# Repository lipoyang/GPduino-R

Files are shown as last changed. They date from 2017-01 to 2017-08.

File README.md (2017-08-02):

GPduino-R
=========

## 概要
GPduino-Rは、ESP8266搭載のWiFiロボット制御ボードです。

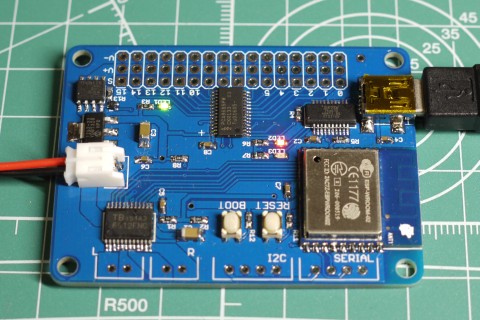
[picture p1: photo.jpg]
写真


以下のことができます。
* ラジコンサーボ最大16個を制御
* DCモータ2個を制御 (最大連続1.2A / 最大瞬間3.0A)
* 電源 3.6V～7.2V (4.8～6V推奨)、電源電圧を監視
* WiFiによる通信　(APにもSTAにもなれる)

## ファイル一覧

* hard/GPduino-R/
	* GPduino-R.sch/brd: 回路/基板設計データ(Eagle形式)
	* GPduino-R.pdf: 回路図(PDF)
	* GPduino-R_BOM.xlsx: BOMリスト(Excel形式)
	* GPduino-R.GBL/GBO/GBP/GBS/GML/GTL/GTO/GTP/GTS/TXT: ガーバデータ
* firm/
	* GPduinoR/: Arduinoライブライリ
	* Mini4LD/Mini4LD.ino: 四足歩行ロボットのArduinoスケッチ
* LICENSE: Apache Licence 2.0です。
	* ただし、回路/基板設計は、Creative Commons Attribution Share-Alike 3.0です。
* README.md これ

## Arduino開発環境のセットアップ
GPduino-R はESP8266を搭載しており、Arduinoでファームウェアを開発できます。

* まず、ArduinoIDE をインストールしておきます。 (ここでは 1.6.9 を使用)
* [ファイル] > [環境設定] > [Additional Boards Manager URLs:]に下記URLをコピペ
	* http://arduino.esp8266.com/stable/package_esp8266com_index.json (安定版)
	* http://arduino.esp8266.com/staging/package_esp8266com_index.json (開発版)
* [ツール] > [ボード] > [ボードマネージャ] で [esp8266] をインストール
* [ツール] > [ボード] で [Generic ESP8266 Module]を選択
	* Flash Mode : QIO
	* Flash Frequency : 40MHz
	* Upload Using : Serial
	* CPU Frequency : 80MHz
	* Flash Size : 4M(3M SPIFFS)　(3MBをファイルシステムで使用 / 1MBをスケッチで使用)
	* Debug port : Disabled
	* Debug Level : None
	* Reset Method : nodemcu
	* Upload Speed : 115200

## Arduinoライブラリのインストール

firm/ にある GPduinoR/ フォルダを、Arduinoのライブラリフォルダにコピーします。

Arduinoのライブラリフォルダは、以下の場所です。
* Documents/Arduino/libraries (Windows10, Mac, Linux)
* My Documents/Arduino/libraries (Windows7)

## Arduinoスケッチの作成
GPduinoR.h をインクルードします。
``` c
#include <GPduinoR.h>
```
すると、以下のオブジェクトが使用できます。詳細は、GPduinoR/フォルダにあるソースを参照してください。
- Battery: バッテリー電圧の取得
- DcMotor: DCモータの制御
- RcServo: ラジコンサーボの制御
- UdpComm: WiFiによるUDP/IP通信

Mini4LD/Mini4LD.ino は、四足歩行ロボット([歩くミニ四駆](https://www.youtube.com/watch?v=Bx3RYRKqrKQ))のArduinoスケッチです。参考にしてください。

## Arduinoスケッチの書き込み

* GPduino-RをUSBケーブルでPCに接続します。
* 書き込み時もUSBからの給電は受けません。CN1から給電してください。
* Windows 7以降であればドライバが自動でインストールされ、COMポートとして認識されます。
	* 自動でデバイスが認識されない環境ではFTDIのデバイスドライバをインストールしてください。
* [ツール] > [シリアルポート]でGPduino-RのCOMポート番号を指定します。
* BOOTボタン(SW2)を押し下げた状態で、RESETボタン(SW1)を押して離します。
* Uploadボタンで、ファームウェアを書き込みます。

## 既知の問題点
* サーボのコネクタの間隔が狭すぎる。(干渉して16個全部を接続できない)

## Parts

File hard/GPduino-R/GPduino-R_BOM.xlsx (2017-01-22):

No | Reference | Part Number | Vender | Description | DNP | Qty | Unit Price | Price | Lot Size | Supplier | Supplier Code
1 | C1,3 | 47u(3216) | (generic) | 3216型 |  | 2 | 30 | 60 | 10 | 秋月 | P-06040
2 | C2,4,5,6,7,8 | 0.1u(1608) | (generic) | 1608型 |  | 6 | 0.325 | 1.95 | 4000 | 秋月 | P-01299
3 | CN1 | S2B-PH-K-S | JST | PH 2極 L型ポスト |  | 1 | 16 | 16 | 1 | 共立 | -
4 | CN2,3 | B2B-EH-A | JST | EH 2極 I型ポスト | DNP | 0 | 16 | 0 | 1 | 共立 | -
5 | CN4 | MINI-USB-UX60A-MB-5ST | HRS | USB ミニB |  | 1 | 50 | 50 | 4 | 秋月 | C-05690
6 | CN5,6 | B4B-EH-A | JST | EH 4極 I型ポスト | DNP | 0 | 21 | 0 | 1 | 共立 | -
7 | CN7,8,9,10 | - | (generic) | ピンヘッダ 3ピン×4 | DNP | 0 | 60 | 0 | 2 | 共立 | -
8 | LED1 | OSYG1608 | OptoSupply | 1608型 GREEN |  | 1 | 10 | 10 | 20 | 秋月 | I-03980
9 | LED2 | OSHR1608 | OptoSupply | 1608型 RED |  | 1 | 10 | 10 | 20 | 秋月 | I-03978
10 | LED3 | OSYL1608 | OptoSupply | 1608型 YELLOW |  | 1 | 10 | 10 | 20 | 秋月 | I-03984
11 | Q1 | DTC014EEB | ROHM | NPNデジタルトランジスタ |  | 1 | 3.2 | 3.2 | 200 | RS | 124-6536
12 | Q2 | TPC8125 | Toshiba | PMOS FET |  | 1 | 36.8 | 36.8 | 5 | RS | 756-3817
13 | R1 | 100k(1608) | (generic) | 1608型 |  | 1 | 0.2 | 0.2 | 2500 | 秋月 | R-06104
14 | R2,5,8,11,12,13 | 10k(1608) | (generic) | 1608型 |  | 6 | 0.2 | 1.2 | 2500 | 秋月 | R-06103
15 | R3 | 220(1608) | (generic) | 1608型 |  | 1 | 0.2 | 0.2 | 2500 | 秋月 | R-06221
16 | R4,R6,R7 | 1k(1608) | (generic) | 1608型 |  | 3 | 0.2 | 0.6 | 2500 | 秋月 | R-06102
17 | R9,R10 | 10k(1608) | (generic) | 1608型 | DNP | 0 | 0.2 | 0 | 2500 | 秋月 | R-06103
18 | SW1,2 | SKRPACE010 | ALPS | 表面実装タクトスイッチ |  | 2 | 20 | 40 | 5 | 秋月 | P-06185
20 | U1 | TC1262-3.3VDB05MP | Microchip | LDO, 3.3V-0.5A, SOT-223型 |  | 1 | 81 | 81 | 1 | RS | 703-7905
21 | U2 | TB6621FNG | Toshiba | Dual DCモータドライバ |  | 1 | 306 | 306 | 1 | RS | 770-3797
22 | U3 | FT231XS | FTDI | USBシリアル変換 |  | 1 | 210 | 210 | 1 | 秋月 | I-06713
23 | U4 | ESP-WROOM-02 | Espressif Systems | ESP8266 WiFiモジュール |  | 1 | 550 | 550 | 1 | 秋月 | M-09607
24 | U5 | PCA9685PW | NXP | PWMドライバ |  | 1 | 262 | 262 | 2 | RS | 727-5649
25 | - | - | Elecrow | 基板 |  | 1 | 260.1 | 260.1 | 10 | Elecrow | -
26 | - | PH2P300L | Marutsu | PH 2極 アッセンブルケーブル |  | 1 | 54 | 54 | 1 | マルツ | -
 |  |  |  |  |  |  | Total | 1963.25

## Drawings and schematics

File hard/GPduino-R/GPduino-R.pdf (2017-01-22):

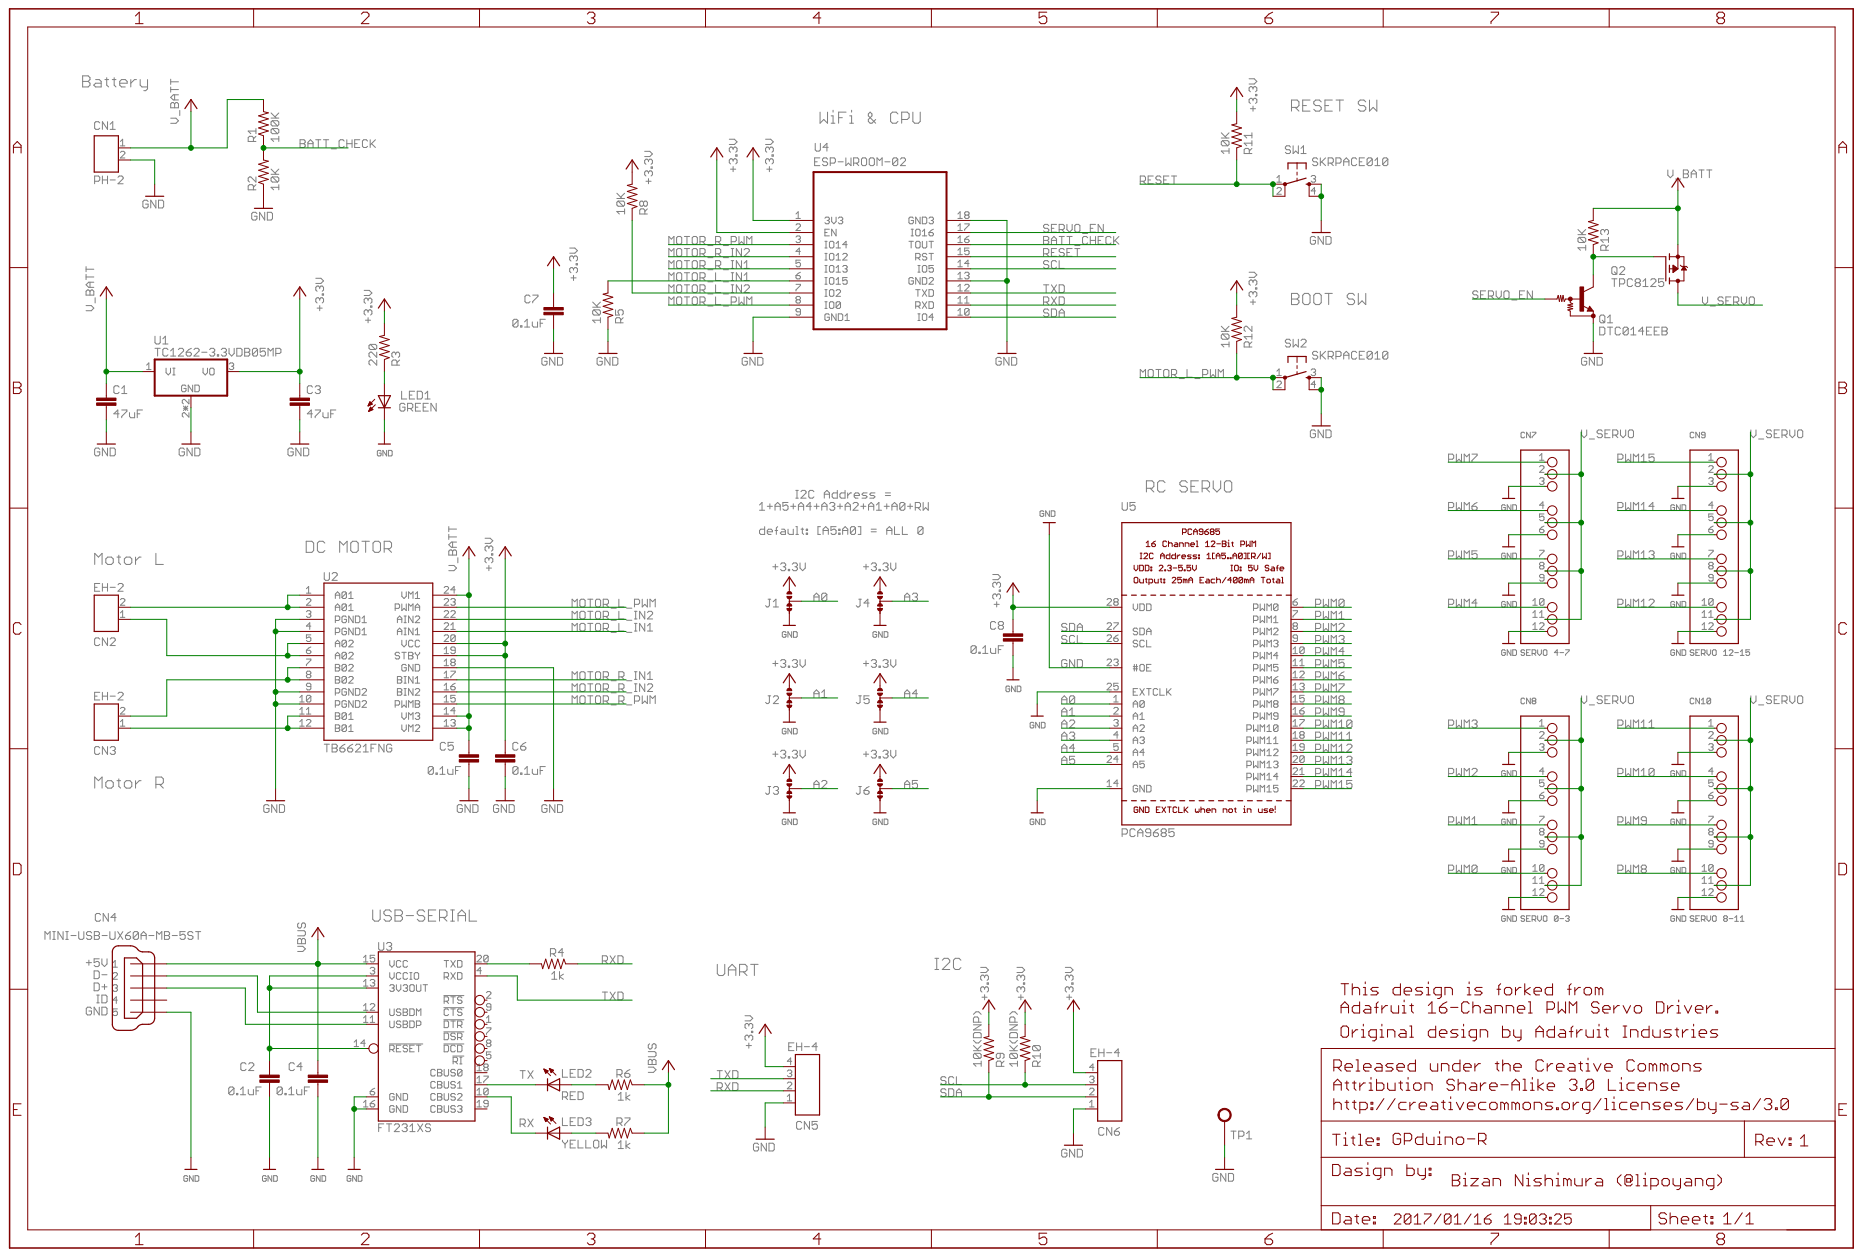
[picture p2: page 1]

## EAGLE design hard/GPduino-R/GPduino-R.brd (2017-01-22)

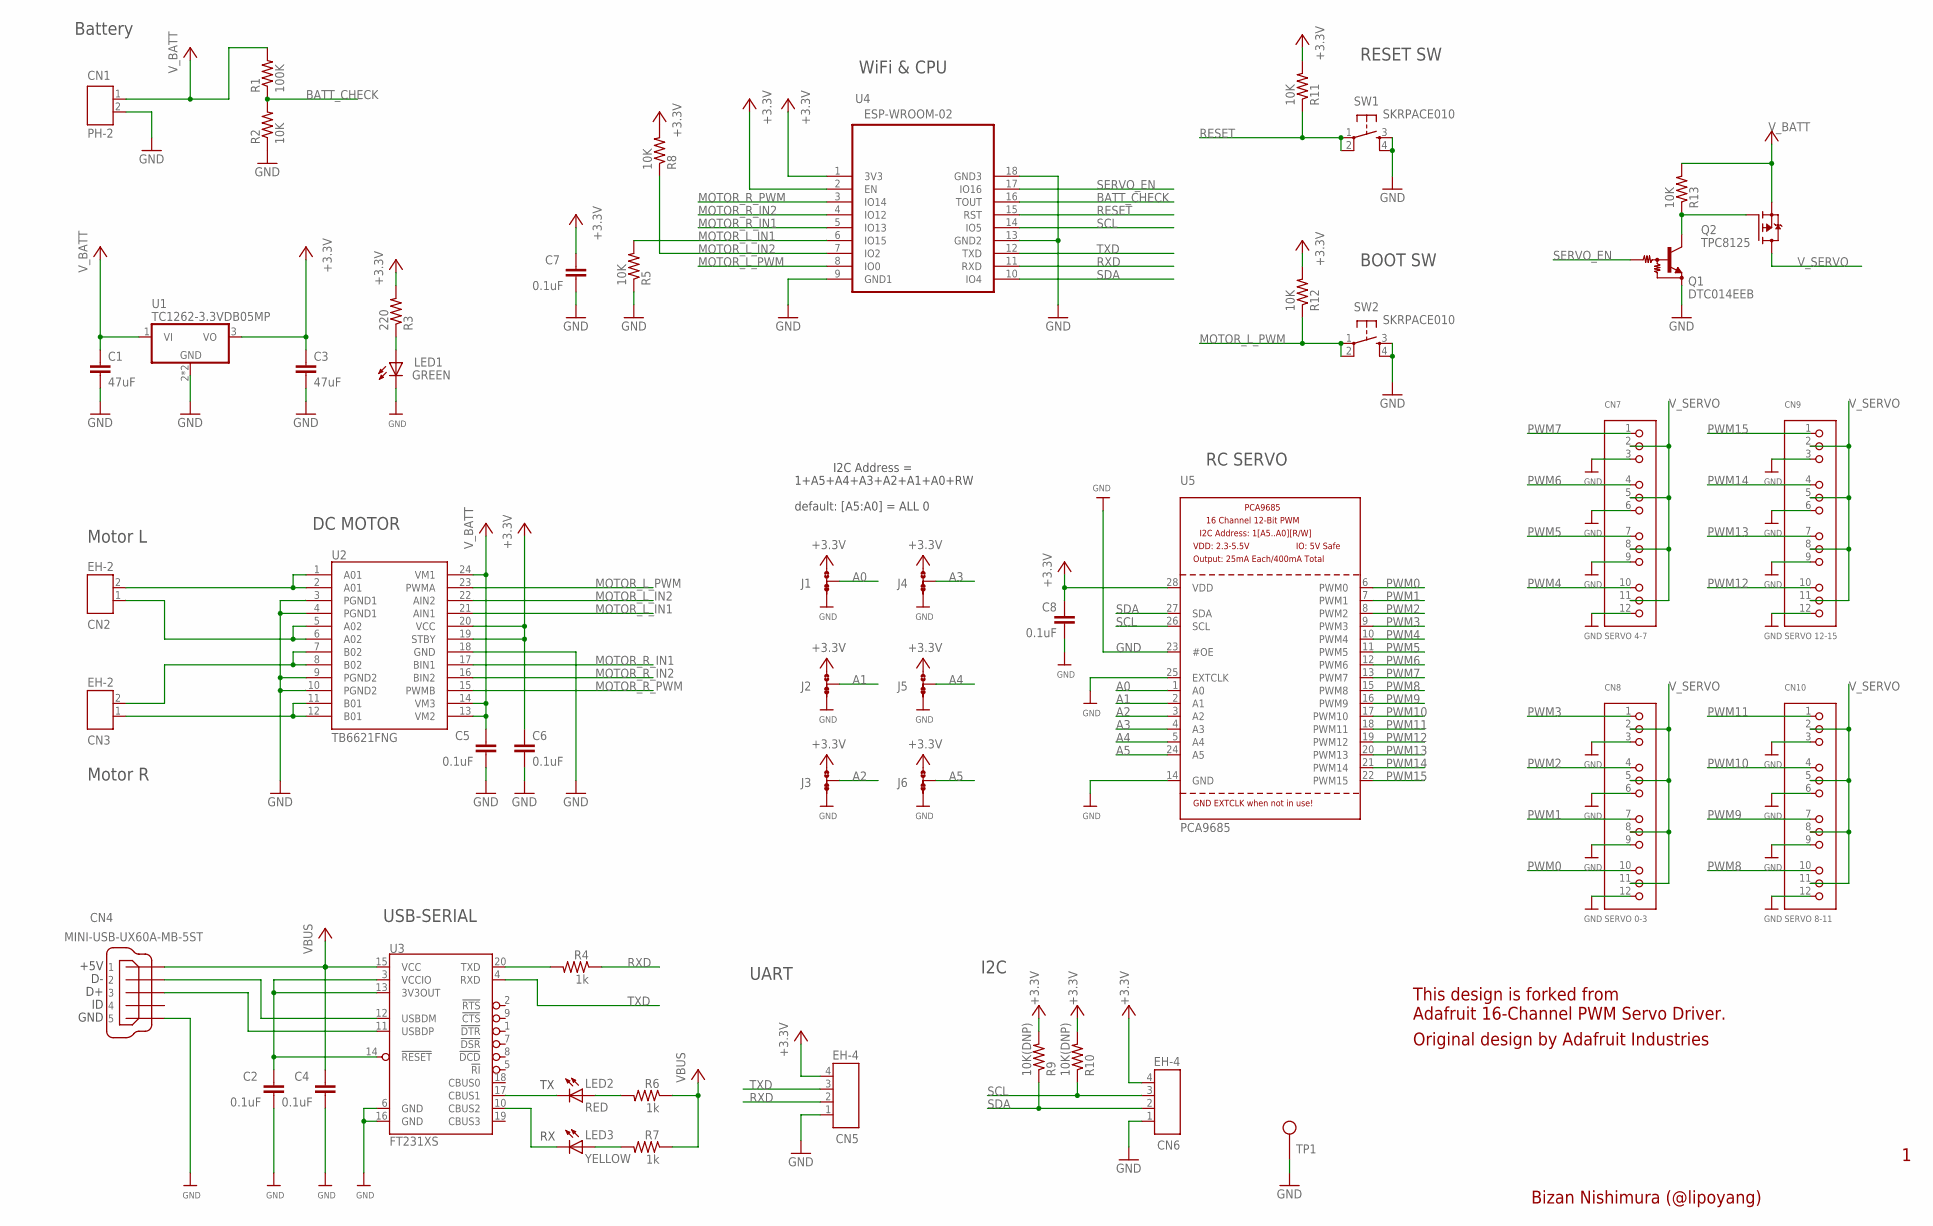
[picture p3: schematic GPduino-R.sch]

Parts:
C1, C3: 47uF; C3216
C2, C4, C5, C6, C7, C8: 0.1uF; C1608
CN1: PH-2
CN2, CN3: EH-2
CN4: MINI-USB-UX60A-MB-5ST; UX60A-MB-5ST
CN5, CN6: EH-4
CN7: SERVO 4-7; 3X04
CN8: SERVO 0-3; 3X04
CN9: SERVO 12-15; 3X04
CN10: SERVO 8-11; 3X04
J1, J2, J3, J4, J5, J6: JUMP-SHORTB; JUMP-SHORT
LED1: GREEN; CHIPLED_0603
LED2: RED; CHIPLED_0603
LED3: YELLOW; CHIPLED_0603
Q1: DTC014EEB; SOT490
Q2: TPC8125; SO-8
R1: 100K; 0603-RES
R2, R5, R8, R11, R12, R13: 10K; 0603-RES
R3: 220; 0603-RES
R4, R6, R7: 1k; 0603-RES
R9, R10: 10K(DNP); 0603-RES
SW1, SW2: SKRPACE010
TP1: TEST_PIN
U1: TC1262-3.3VDB05MP; SOT223
U2: TB6621FNG; SSOP24
U3: FT231XS; SSOP20
U4: ESP-WROOM-02; FRONT-FACE
U5: PCA9685; TSSOP28

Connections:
+3V3: C3.1, C6.1, C7.1, C8.1, CN5.4, CN6.4, J1.1, J2.1, J3.1, J4.1, J5.1, J6.1, R3.2, R8.2, R9.2, R10.2, R11.2, R12.2, U1.3 (VO), U2.19 (STBY), U2.20 (VCC), U4.1 (3V3), U4.2 (EN), U5.28 (VDD)
A0: J1.2, U5.1 (A0)
A01: CN2.2, U2.1 (A01), U2.2 (A01)
A1: J2.2, U5.2 (A1)
A02: CN2.1, U2.5 (A02), U2.6 (A02)
A2: J3.2, U5.3 (A2)
A3: J4.2, U5.4 (A3)
A4: J5.2, U5.5 (A4)
A5: J6.2, U5.24 (A5)
BATT_CHECK: R1.1, R2.2, U4.16 (TOUT)
GND: C1.2, C2.2, C3.2, C4.2, C5.2, C6.2, C7.2, C8.2, CN1.2, CN4.5, CN5.1, CN6.1, CN7.3, CN7.6, CN7.9, CN7.12, CN8.3, CN8.6, CN8.9, CN8.12, CN9.3, CN9.6, CN9.9, CN9.12, CN10.3, CN10.6, CN10.9, CN10.12, J1.3, J2.3, J3.3, J4.3, J5.3, J6.3, LED1.C, Q1.2 (E), R2.1, R5.1, SW1.3, SW1.4, SW2.3, SW2.4, TP1.1, U1.2 (GND), U1.4 (GND), U2.3 (PGND1), U2.4 (PGND1), U2.9 (PGND2), U2.10 (PGND2), U2.18 (GND), U3.6 (GND), U3.16 (GND), U4.9 (GND1), U4.13 (GND2), U4.18 (GND3), U5.14 (GND), U5.23 (#OE), U5.25 (EXTCLK)
MOTOR_L_IN1: R5.2, U2.21 (AIN1), U4.6 (IO15)
MOTOR_L_IN2: R8.1, U2.22 (AIN2), U4.7 (IO2)
MOTOR_L_PWM: R12.1, SW2.1, SW2.2, U2.23 (PWMA), U4.8 (IO0)
MOTOR_R_IN1: U2.17 (BIN1), U4.5 (IO13)
MOTOR_R_IN2: U2.16 (BIN2), U4.4 (IO12)
MOTOR_R_PWM: U2.15 (PWMB), U4.3 (IO14)
unnamed: LED1.A, R3.1
unnamed: R4.2, U3.20 (TXD)
unnamed: CN3.1, U2.11 (B01), U2.12 (B01)
unnamed: CN3.2, U2.7 (B02), U2.8 (B02)
unnamed: LED2.C, U3.17 (CBUS1)
unnamed: LED3.C, U3.10 (CBUS2)
unnamed: LED2.A, R6.2
unnamed: LED3.A, R7.2
unnamed: CN4.2, U3.12 (USBDM)
unnamed: CN4.3, U3.11 (USBDP)
unnamed: C2.1, U3.3 (VCCIO), U3.13 (3V3OUT), U3.14 (!RESET)
unnamed: Q1.3 (C), Q2.4 (G), R13.1
PWM0: CN8.10, U5.6 (PWM0)
PWM1: CN8.7, U5.7 (PWM1)
PWM2: CN8.4, U5.8 (PWM2)
PWM3: CN8.1, U5.9 (PWM3)
PWM4: CN7.10, U5.10 (PWM4)
PWM5: CN7.7, U5.11 (PWM5)
PWM6: CN7.4, U5.12 (PWM6)
PWM7: CN7.1, U5.13 (PWM7)
PWM8: CN10.10, U5.15 (PWM8)
PWM9: CN10.7, U5.16 (PWM9)
PWM10: CN10.4, U5.17 (PWM10)
PWM11: CN10.1, U5.18 (PWM11)
PWM12: CN9.10, U5.19 (PWM12)
PWM13: CN9.7, U5.20 (PWM13)
PWM14: CN9.4, U5.21 (PWM14)
PWM15: CN9.1, U5.22 (PWM15)
RESET: R11.1, SW1.1, SW1.2, U4.15 (RST)
RXD: CN5.2, R4.1, U4.11 (RXD)
SCL: CN6.3, R10.1, U4.14 (IO5), U5.26 (SCL)
SDA: CN6.2, R9.1, U4.10 (IO4), U5.27 (SDA)
SERVO_EN: Q1.1 (B), U4.17 (IO16)
TXD: CN5.3, U3.4 (RXD), U4.12 (TXD)
VBUS: C4.1, CN4.1, R6.1, R7.1, U3.15 (VCC)
V_BATT: C1.1, C5.1, CN1.1, Q2.1 (S), Q2.2 (S), Q2.3 (S), R1.2, R13.2, U1.1 (VI), U2.13 (VM2), U2.14 (VM3), U2.24 (VM1)
V_SERVO: CN7.2, CN7.5, CN7.8, CN7.11, CN8.2, CN8.5, CN8.8, CN8.11, CN9.2, CN9.5, CN9.8, CN9.11, CN10.2, CN10.5, CN10.8, CN10.11, Q2.5 (D), Q2.6 (D), Q2.7 (D), Q2.8 (D)

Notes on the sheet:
Battery
Motor L
Bizan Nishimura (@lipoyang)
Motor R
I2C
1+A5+A4+A3+A2+A1+A0+RW
I2C Address =
default: [A5:A0] = ALL 0
UART
USB-SERIAL
DC MOTOR
RC SERVO
WiFi & CPU
RESET SW
BOOT SW
This design is forked from Adafruit 16-Channel PWM Servo Driver.
Original design by Adafruit Industries

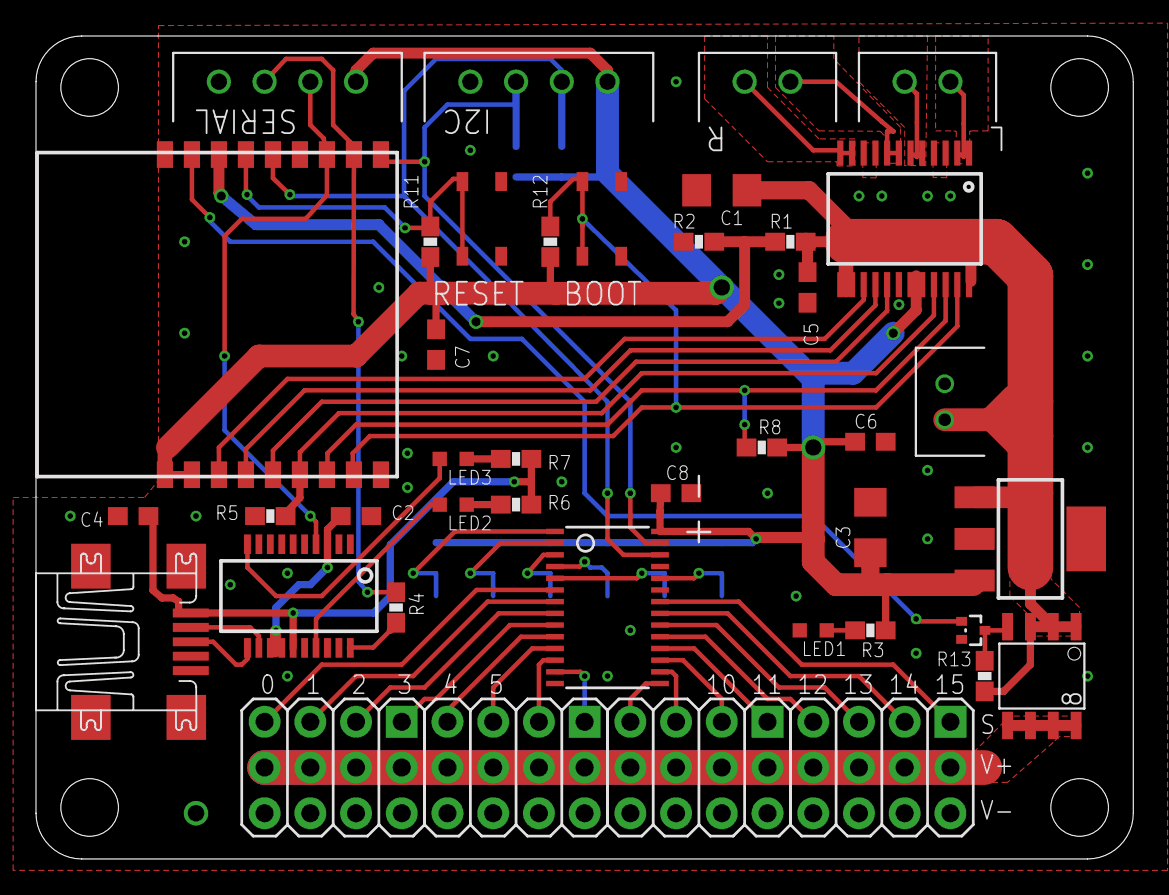
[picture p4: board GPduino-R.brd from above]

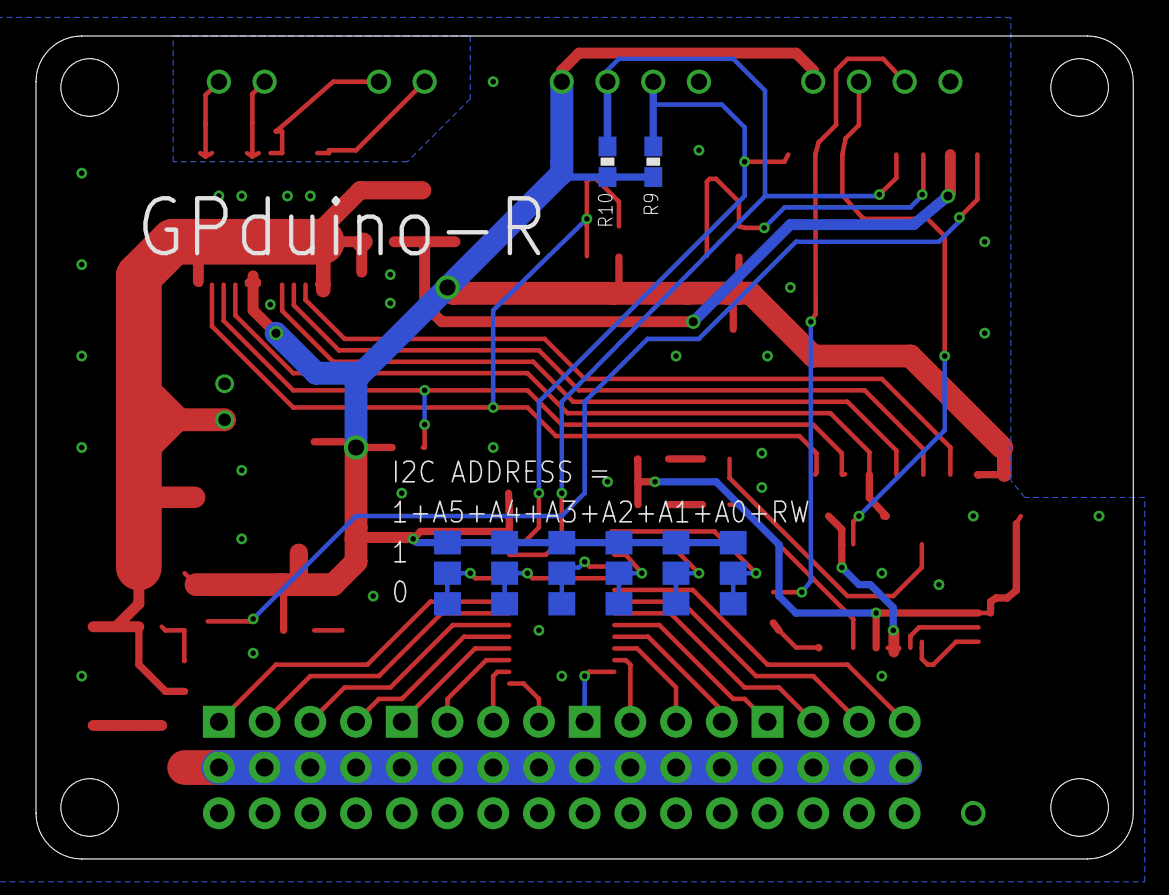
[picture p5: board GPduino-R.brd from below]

Board: 2 copper layers, 61.0 x 45.7 mm, 50 parts (8 on the bottom side), 54 nets.

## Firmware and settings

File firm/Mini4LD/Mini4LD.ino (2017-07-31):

#include <GPduinoR.h>

// サーボ番号
enum {
    SERVO_RF_Y = 0, // 右前股
    SERVO_RF_Z,     // 右前膝
    SERVO_LF_Y,     // 左前股
    SERVO_LF_Z,     // 左前膝
    SERVO_RB_Y,     // 右後股
    SERVO_RB_Z,     // 右後膝
    SERVO_LB_Y,     // 左後股
    SERVO_LB_Z,     // 左後膝
};
// サーボチャンネル開始番号
#define SERVO_BEGIN 8

// サーボの向きとゼロ点オフセット
static const int SERVO_POLARITY[]={
// 0:右前股 1:右前膝 2:左前股 3:左前膝 4:右後股 5:右後膝 6:左後股 7:左後膝
  -1,      -1,      +1,      +1,      -1,      +1,      +1,      -1
};
static const int SERVO_OFFSET[]={
// 0:右前股 1:右前膝 2:左前股 3:左前膝 4:右後股 5:右後膝 6:左後股 7:左後膝
  18,       0,     -14,       3,     -17,     -13,      22,       5
};

// 1コマの時間[msec]
#define T_ORBIT 0//1//5//10
int t_orbit = 10; 

// 軌道テーブルのコマ数
#define N_TABLE 16
// 軌道テーブルの補間コマ数
#define N_INTERPOL 8
// 軌道の一周コマ数
#define N_ORBIT (N_TABLE * N_INTERPOL)
// 軌道の半周期のコマ数
#define N_HALF  (N_ORBIT/2)
// 歩きはじめ軌道のコマ数
#define N_ORBIT0 24

// 軌道テーブル(股)
const float Y_ORBIT[] = {
//     0    1    2    3    4    5    6    7    8    9   10   11   12   13   14   15 (コマ番号)
//    25,  15,   5,  -5, -15, -25, -25, -25, -25, -15,  -5,   5,  15,  25,  25,  25
       0, -10, -20, -25, -25, -25, -20, -10,   0,  10,  20,  25,  25,  25,  20,  10 // (1)
//     0,  -8, -16, -24, -24, -24, -16,  -8,   0,   8,  16,  24,  24,  24,  16,   8 // (2)
};
// 軌道テーブル(膝)
const float Z_ORBIT[] = {
//     0    1    2    3    4    5    6    7    8    9   10   11   12   13   14   15 (コマ番号)
//    10,  10,  10,  10,  10,  10,  15,  20,  25,  25,  25,  25,  25,  25,  20,  15
      10,  10,  10,  13,  18,  23,  26,  26,  26,  26,  26,  23,  18,  13,  10,  10 // (1)
//    10,  10,  10,  10,  18,  26,  26,  26,  26,  26,  26,  26,  18,  10,  10,  10 // (2)
};
// 軌道テーブル(膝) 歩きはじめ/歩きおわり用
const float Z0_ORBIT[] = {
//     0    1    2    3    4(コマ番号)
      10,  15,  20,  26,  26
};

// 軌道の位相(コマ数)
static int phase;

// 歩行方向 (前後方向)
static int walk_dir;

// 停止指令フラグ
static bool to_stop;

// 左右の歩幅倍率
static float r_step; // 右側歩幅指令値
static float l_step; // 左側歩幅指令値
static float rf_step, rb_step, lf_step, lb_step; // 各足の現在の歩幅
// 旋回時の歩幅倍率
#define STEP_LONG   1.5
#define STEP_SHORT  0.25

// 歩行状態
static int walk_state;
#define STATE_STOP      0   //停止状態
#define STATE_STARTING  1   //歩きはじめ状態
#define STATE_WALKING   2   //歩行状態
#define STATE_STOPPING  3   //歩きおわり状態

// プロポ状態保持用
static int g_fb;
static int g_lr;

// 送信バッファ
static char txbuff[256];
// 3.5V未満でローバッテリーとする
// (3.5V / 11) / 1.0V * 1024 =  325
#define LOW_BATTERY    325

/**
 * バッテリー電圧チェック
 */
void battery_check()
{
    static char txbuff[256];
    
    if(!UdpComm.isReady()) return;
    
    static int cnt1 = 0;
    static int cnt2 = 0;
    
    cnt1++;
    if(cnt1 < 10000) return;
    cnt1 = 0;

    unsigned short Vbat_ave = 500;//Battery.getAdc();
    //Serial.print("Vbat_ave");Serial.println(Vbat_ave);

    // 1秒ごとに電圧値送信
    cnt2++;
    if(cnt2 >= 10)
    {
        cnt2=0;
        
        txbuff[0]='#';
        txbuff[1]='B';
        Uint16ToHex(&txbuff[2], Vbat_ave, 3);
        txbuff[5]='$';
        txbuff[6]='\0';
        UdpComm.send(txbuff);
    }
}

// 軌道の補間
float orbit_interpol(const float* orbit, int phase)
{
    int n = phase / N_INTERPOL;
    int m = phase % N_INTERPOL;
    
    float x1 = orbit[n];
    n++;
    if(n>=N_TABLE) n=0;
    float x2 = orbit[n];
    
    float x = x1 + (x2-x1) * m / N_INTERPOL;
    
    return x;
}

// 初期設定
void setup() {
    Serial.begin(115200);
    delay(100);

    // UDP通信の設定
    UdpComm.beginAP(NULL, "12345678");
    //UdpComm.beginSTA("SSID", "password", "gpduino");
    UdpComm.onReceive = UdpComm_callback;

    // サーボ初期値設定
    RcServo.begin();
    for(int i=0;i<8;i++){
        RcServo.setPolarity(SERVO_BEGIN+i, SERVO_POLARITY[i]);
        RcServo.setOffset  (SERVO_BEGIN+i, SERVO_OFFSET[i]);
    }
    RcServo.out(SERVO_BEGIN+SERVO_RF_Y, orbit_interpol(Y_ORBIT, 0));
    RcServo.out(SERVO_BEGIN+SERVO_RF_Z, orbit_interpol(Z_ORBIT, 0));
    RcServo.out(SERVO_BEGIN+SERVO_LF_Y, orbit_interpol(Y_ORBIT, 0));
    RcServo.out(SERVO_BEGIN+SERVO_LF_Z, orbit_interpol(Z_ORBIT, 0));
    RcServo.out(SERVO_BEGIN+SERVO_RB_Y, orbit_interpol(Y_ORBIT, 0));
    RcServo.out(SERVO_BEGIN+SERVO_RB_Z, orbit_interpol(Z_ORBIT, 0));
    RcServo.out(SERVO_BEGIN+SERVO_LB_Y, orbit_interpol(Y_ORBIT, 0));
    RcServo.out(SERVO_BEGIN+SERVO_LB_Z, orbit_interpol(Z_ORBIT, 0));
    RcServo.powerOn();
    
    Battery.begin();
  
    phase = 0;
    walk_dir = 0;
    r_step = 1.0;
    l_step = 1.0;
    rf_step = r_step;
    rb_step = r_step;
    lf_step = l_step;
    lb_step = l_step;
    walk_state = STATE_STOP;
    to_stop = false;
    
    g_fb = 0;
    g_lr = 0;
}

// メインループ
void loop() {
    
    // バッテリーチェック
    battery_check();
    
    // UDP通信
    UdpComm.loop();
    
    int phase180; // 半周期ずれ位相
    
    switch(walk_state)
    {
    // 停止状態
    case STATE_STOP:
        if( walk_dir != 0){
            walk_state = STATE_STARTING;
            phase = 0;
        }
        break;
        
    // 歩きはじめ状態
    case STATE_STARTING:
        RcServo.out(SERVO_BEGIN+SERVO_RF_Y, 0);
        RcServo.out(SERVO_BEGIN+SERVO_RF_Z, orbit_interpol(Z0_ORBIT, 0));
        RcServo.out(SERVO_BEGIN+SERVO_LF_Y, 0);
        RcServo.out(SERVO_BEGIN+SERVO_LF_Z, orbit_interpol(Z0_ORBIT, phase));
        RcServo.out(SERVO_BEGIN+SERVO_RB_Y, 0);
        RcServo.out(SERVO_BEGIN+SERVO_RB_Z, orbit_interpol(Z0_ORBIT, phase));
        RcServo.out(SERVO_BEGIN+SERVO_LB_Y, 0);
        RcServo.out(SERVO_BEGIN+SERVO_LB_Z, orbit_interpol(Z0_ORBIT, 0));
        
        phase++;
        if(phase >  N_ORBIT0){
            phase = 0;
            walk_state = STATE_WALKING;
        }
        delay(t_orbit);//T_ORBIT);
        break;
        
    // 歩きおわり状態
    case STATE_STOPPING:
        RcServo.out(SERVO_BEGIN+SERVO_RF_Y, 0);
        RcServo.out(SERVO_BEGIN+SERVO_RF_Z, orbit_interpol(Z0_ORBIT, 0));
        RcServo.out(SERVO_BEGIN+SERVO_LF_Y, 0);
        RcServo.out(SERVO_BEGIN+SERVO_LF_Z, orbit_interpol(Z0_ORBIT, N_ORBIT0-phase));
        RcServo.out(SERVO_BEGIN+SERVO_RB_Y, 0);
        RcServo.out(SERVO_BEGIN+SERVO_RB_Z, orbit_interpol(Z0_ORBIT, N_ORBIT0-phase));
        RcServo.out(SERVO_BEGIN+SERVO_LB_Y, 0);
        RcServo.out(SERVO_BEGIN+SERVO_LB_Z, orbit_interpol(Z0_ORBIT, 0));
        
        phase++;
        if(phase >  N_ORBIT0){
            walk_state = STATE_STOP;
        }
        delay(t_orbit);//T_ORBIT);
        break;
        
    // 歩行状態
    case STATE_WALKING:
        if( to_stop && (phase == 0)){
            walk_state = STATE_STOPPING;
            phase = 0;
            walk_dir = 0;
            to_stop = false;
            break;
        }
        phase180 = ((phase+N_HALF) % N_ORBIT);
        // 歩幅更新タイミング
        if(phase == 0){
            rf_step = r_step;
            lb_step = l_step;
        }
        if(phase180 == 0){
            lf_step = l_step;
            rb_step = r_step;
        }
        RcServo.out(SERVO_BEGIN+SERVO_RF_Y, orbit_interpol(Y_ORBIT, phase   ) * rf_step);
        RcServo.out(SERVO_BEGIN+SERVO_RF_Z, orbit_interpol(Z_ORBIT, phase   ));
        RcServo.out(SERVO_BEGIN+SERVO_LF_Y, orbit_interpol(Y_ORBIT, phase180) * lf_step);
        RcServo.out(SERVO_BEGIN+SERVO_LF_Z, orbit_interpol(Z_ORBIT, phase180));
        RcServo.out(SERVO_BEGIN+SERVO_RB_Y, orbit_interpol(Y_ORBIT, phase180) * rb_step);
        RcServo.out(SERVO_BEGIN+SERVO_RB_Z, orbit_interpol(Z_ORBIT, phase180));
        RcServo.out(SERVO_BEGIN+SERVO_LB_Y, orbit_interpol(Y_ORBIT, phase   ) * lb_step);
        RcServo.out(SERVO_BEGIN+SERVO_LB_Z, orbit_interpol(Z_ORBIT, phase   ));
        
        // 前進ないし後退
        if( walk_dir > 0 )
        {
            phase++;
            if(phase >=  N_ORBIT) phase = 0;
        }else{
            phase--;
            if(phase < 0) phase = N_ORBIT - 1;
        }
        
        delay(t_orbit);//T_ORBIT);
        break;
        
    // 異常な場合
    default:
        walk_state = STATE_STOP;
        break;
    }
}

void propo_ctrl()
{
    if(g_fb > 32){
        // 前進
        walk_dir = 1;
        to_stop = false;
        t_orbit = -((g_fb-31)*10)/96+10;
        if(t_orbit < 0) t_orbit = 0;
    }else if(g_fb < -32){
        // 後退
        walk_dir = -1;
        to_stop = false;
        t_orbit = ((g_fb+31)*10)/96+10;
        if(t_orbit < 0) t_orbit = 0;
    }else{
        // 停止
        to_stop = true;
    }
    
    if(g_fb != 0){
      if(g_lr > 64){
          // 右旋回
          r_step = STEP_SHORT;
          l_step = STEP_LONG;
      }else if(g_lr < -64){
          // 左旋回
          r_step = STEP_LONG;
          l_step = STEP_SHORT;
      }else{
          // 中立
          r_step = 1.0;
          l_step = 1.0;
      }
      //servo_ctrl(0);
    }else{
      if(g_lr > 64){
          // 右旋回
          r_step = STEP_SHORT;
          l_step = STEP_LONG;
          walk_dir = 1;
          to_stop = false;
      }else if(g_lr < -64){
          // 左旋回
          r_step = STEP_LONG;
          l_step = STEP_SHORT;
         walk_dir = 1;
        to_stop = false;
     }else{
          // 中立
          r_step = 1.0;
          l_step = 1.0;
          // 停止
          to_stop = true;
      }
      //servo_ctrl(g_lr);
    }
}

/**
 * 受信したコマンドの実行
 *
 * @param buff 受信したコマンドへのポインタ
 */
void UdpComm_callback(char* buff)
{
    int servoNum;
    unsigned short val;
    uint16_t pulselen;
    
    if(buff[0] != '#') return;
    buff++;
    
    switch(buff[0])
    {
    /* テスト:サーボコマンド */
    case 'S':
        // 全サーボ制御コマンド
        if(buff[1] == 'A')
        {
            for(servoNum=0; servoNum<8; servoNum++){
                if( HexToUint16(&buff[2+servoNum*2], &val, 2) == 0 ){
                    if(val <= 180){
                        RcServo.out(servoNum, (int)val - 90);
                    }
                }
            }
        }
        // テスト:個別サーボ制御コマンド
        else
        {
            servoNum = buff[1] - '0';
            if(servoNum < 8){
                if( HexToUint16(&buff[2], &val, 2) == 0 ){
                    if(val <= 180){
                        RcServo.out(servoNum, (int)val - 90);
                    }
                }
            }
        }
        break;
    
    /* テスト:歩行コマンド */
    case 'W':
        // 左右方向
        switch(buff[1]){
        // 左旋回
        case 'L':
            r_step = STEP_LONG;
            l_step = STEP_SHORT;
            break;
        // 右旋回
        case 'R':
            r_step = STEP_SHORT;
            l_step = STEP_LONG;
            break;
        // 直進
        case 'N':
            r_step = 1.0;
            l_step = 1.0;
            break;
        }
        // 前後方向
        switch(buff[2]){
        // 前進
        case 'F':
            walk_dir = 1;
            to_stop = false;
            break;
        // 後退
        case 'B':
            walk_dir = -1;
            to_stop = false;
            break;
        // 停止
        case 'N':
            // walk_dir = 0;
            to_stop = true;
            break;
        }
        break;
    
    /* GPduino標準コマンド */
    
    /* Dコマンド(前進/後退)
       書式: #Dxx$
       xx: 0のとき停止、正のとき前進、負のとき後退。
     */
    case 'D':
        // 値の解釈
        if( HexToUint16(&buff[1], &val, 2) != 0 ) break;
        g_fb = (int)((signed char)val);
        propo_ctrl();
        break;
        
    /* Tコマンド(旋回)
       書式: #Txx$
       xx: 0のとき中立、正のとき右旋回、負のとき左旋回
     */
    case 'T':
        // 値の解釈
        if( HexToUint16(&buff[1], &val, 2) != 0 ) break;
        g_lr = (int)((signed char)val);
        propo_ctrl();
        break;
    }
}

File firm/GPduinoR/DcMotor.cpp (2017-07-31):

#include <Arduino.h>

#define _DC_MOTOR_C_
#include <DcMotor.h>

// Pin Number
#define MOTOR_R_PWM    14
#define MOTOR_R_IN2    12
#define MOTOR_R_IN1    13
#define MOTOR_L_PWM    0
#define MOTOR_L_IN2    2
#define MOTOR_L_IN1    15

// begin the DC motor driver
void DcMotor_t::begin()
{
    // initialize PWM
    analogWrite(MOTOR_L_PWM, 0);
    analogWrite(MOTOR_R_PWM, 0);
    
    // initialize GPIO
    digitalWrite(MOTOR_L_IN1, LOW);
    digitalWrite(MOTOR_L_IN2, LOW);
    digitalWrite(MOTOR_R_IN1, LOW);
    digitalWrite(MOTOR_R_IN2, LOW);
    pinMode(MOTOR_L_IN1, OUTPUT);
    pinMode(MOTOR_L_IN2, OUTPUT);
    pinMode(MOTOR_R_IN1, OUTPUT);
    pinMode(MOTOR_R_IN2, OUTPUT);
}

// drive the motor
// ch: channel. MOTOR_LEFT(=0) or MOTOR_RIGHT(=1)
// value: output value (-1023 to +1023)
void DcMotor_t::out(int ch, int value)
{
    static const int IN1[]={MOTOR_L_IN1, MOTOR_R_IN1};
    static const int IN2[]={MOTOR_L_IN2, MOTOR_R_IN2};
    static const int PWM[]={MOTOR_L_PWM, MOTOR_R_PWM};
    
    int lpwm,rpwm,lin1,lin2,rin1,rin2;
    
    int pwm = abs(value);
    if(pwm<0) pwm = 0;
    if(pwm>1023) pwm = 1023;
    
    int in1,in2;
    if(value > 0){
        in1 = LOW;
        in2 = HIGH;
    }else if(value < 0){
        in1 = HIGH;
        in2 = LOW;
    }else{
        in1 = LOW;
        in2 = LOW;
        pwm = 0;
    }

    digitalWrite(IN1[ch], in1);
    digitalWrite(IN2[ch], in2);
    analogWrite(PWM[ch], pwm);
}

// drive the both motors (as a tank)
// common: common output of both motors, or translation (-1023 to +1023)
// diff: differential output of both motors, or rotation (-1023 to + 1023)
void DcMotor_t::outDiff(int common, int diff)
{
    int l,r;
    
    l = common + diff;
    r = common - diff;
    
    if(l> 1023) l= 1023;
    if(l<-1023) l=-1023;
    if(r> 1023) r= 1023;
    if(r<-1023) r=-1023;
    
    this->out(MOTOR_LEFT,  l);
    this->out(MOTOR_RIGHT, r);
}

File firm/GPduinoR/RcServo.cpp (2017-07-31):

#define _RC_SERVO_C_
#include <RcServo.h>
#include <EEPROM.h>

// Pin Number
#define SERVO_POWON    16

// pulth width = 0.5ms to 2.5ms (neutral position = 1.5ms)
#define PULSE_MIN  102 // 102/4096 * 20ms = 0.5ms
#define PULSE_MAX  512 // 512/4096 * 20ms = 2.5ms

// begin the RC servo driver
void RcServo_t::begin()
{
    // turn off the power of all servos
    digitalWrite(SERVO_POWON, LOW);
    pinMode(SERVO_POWON, OUTPUT);
    
    // setup PCA9685 PWM driver
    Pwm.begin();
    Pwm.setPWMFreq(50);  // cycle = 20msec
}

// turn on the power of all servos
void RcServo_t::powerOn()
{
    digitalWrite(SERVO_POWON, HIGH);
}

// turn off the power of all servos
void RcServo_t::powerOff()
{
    digitalWrite(SERVO_POWON, LOW);
}

// control the servo
// ch: channel
// value: output value (-90 to +90 [deg])
void RcServo_t::out(int ch, int value)
{
    // convert (-90,+90)[deg] -> (0,180)[deg] with offset and polarity
    uint32_t deg = 90 + Offset[ch] + Polarity[ch] * value;
    // convet deg value -> timer count value
    uint16_t cnt = PULSE_MIN + (uint16_t)(deg*(PULSE_MAX-PULSE_MIN)/180);
    
    Pwm.setPWM(ch, 0, cnt);
}

// set polarity
// ch: channel
// polarity: polarity of output (+1 or -1)
void RcServo_t::setPolarity(int ch, int polarity)
{
    Polarity[ch] = polarity;
}

// set offset
// ch: channel
// offset: offset of output
void RcServo_t::setOffset(int ch, int offset)
{
    Offset[ch] = offset;
}

// get polarity
int* RcServo_t::getPolarity()
{
    return Polarity;
}

// get offset
int* RcServo_t::getOffset()
{
    return Offset;
}

// save settings
// base: base address of EEPROM
void RcServo_t::saveSettings(int base)
{
    int ch;
    for(ch=0; ch<SERVO_NUM; ch++){
        EEPROM.write(base + ch*2 + 0, Polarity[ch]);
        EEPROM.write(base + ch*2 + 1, Offset  [ch]);
    }
    EEPROM.commit();
}

// load settings
// base: base address of EEPROM
void RcServo_t::loadSettings(int base)
{
    int ch;
    for(ch=0; ch<SERVO_NUM; ch++){
        Polarity[ch] = (int)((signed char)EEPROM.read(base + ch*2 + 0));
        Offset  [ch] = (int)((signed char)EEPROM.read(base + ch*2 + 1));
    }
}

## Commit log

2017-01-22 ファイル追加
    [GPduino-R.GBL, GPduino-R.GBO, GPduino-R.GBP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]
2017-07-31 ファームウェアを追加
2017-08-01 READMEの修正

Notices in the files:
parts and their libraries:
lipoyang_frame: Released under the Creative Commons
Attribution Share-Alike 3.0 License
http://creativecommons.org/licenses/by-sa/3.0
